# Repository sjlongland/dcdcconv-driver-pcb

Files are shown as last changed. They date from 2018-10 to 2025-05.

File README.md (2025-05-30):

[Find this project on codeberg](https://codeberg.org/sjlongland/dcdcconv-driver-pcb)

As a result of Github's decision to force AI-generated issues with no opt-out,
I am migrating personal projects of mine to Codeberg.  The project at Github
will be archived.

----

# PWM MOSFET driver board

This is a LVDS-compatible MOSFET driver board for use with the [DC-DC converter
board](https://codeberg.org/sjlongland/dcdcconv-controller-pcb).  It can drive
two N-Channel MOSFETs, either mounting the leads through the supplied
connection points `J3` and `J4` (suitable for TO-220 size MOSFETs) or via short
connection cables.  Due to parasitic inductance, it is best these be kept as
short as practical.

## Parts list

* U1: TI DS90C402 dual-channel LVDS receiver
* U2: TI UCC27212A-Q1 high/low side N-MOSFET driver
* U3: 74AHC04 (SOIC-14) hex inverting buffer (U1 when not connected to a LVDS
  source will drive both its outputs high, this inverts this to ensure both MOSFETs
  remain off in this condition.)
* C2: ≥100µF ≥10V electrolytic capacitor 6.3mm SMD (Bulk 5V rail decoupling)
* C1, C10: 100nF ≥10V ceramic capacitor 0805 SMD (local decoupling for U1, U3)
* C3: ≥100µF ≥20V electrolytic capacitor 6.3mm SMD (Bulk 12V rail decoupling)
* C4: 100nF ≥20V ceramic capacitor 0805 SMD (local decoupling for U2)
* C5: Bootstrap electrolyic capacitor for U2, refer to data sheet.  6.3mm SMD.
* J1: 6-pin 2.54mm "KK" connector (LVDS input and 5V rail)
* J2: 2-pin 2.54mm "KK" connector (12V rail)
* J3, J4: 3-pin 2.54mm "KK" connector or TO-220 size MOSFETs with heatsinks.
* (**FIT ONE ONLY**) C6, C7, C8, C9: ~100pF ≥20V ceramic capacitor 0805 (0V AC
  de-coupling to chassis.  Choose the one that best suits your mounting
  requirements.)

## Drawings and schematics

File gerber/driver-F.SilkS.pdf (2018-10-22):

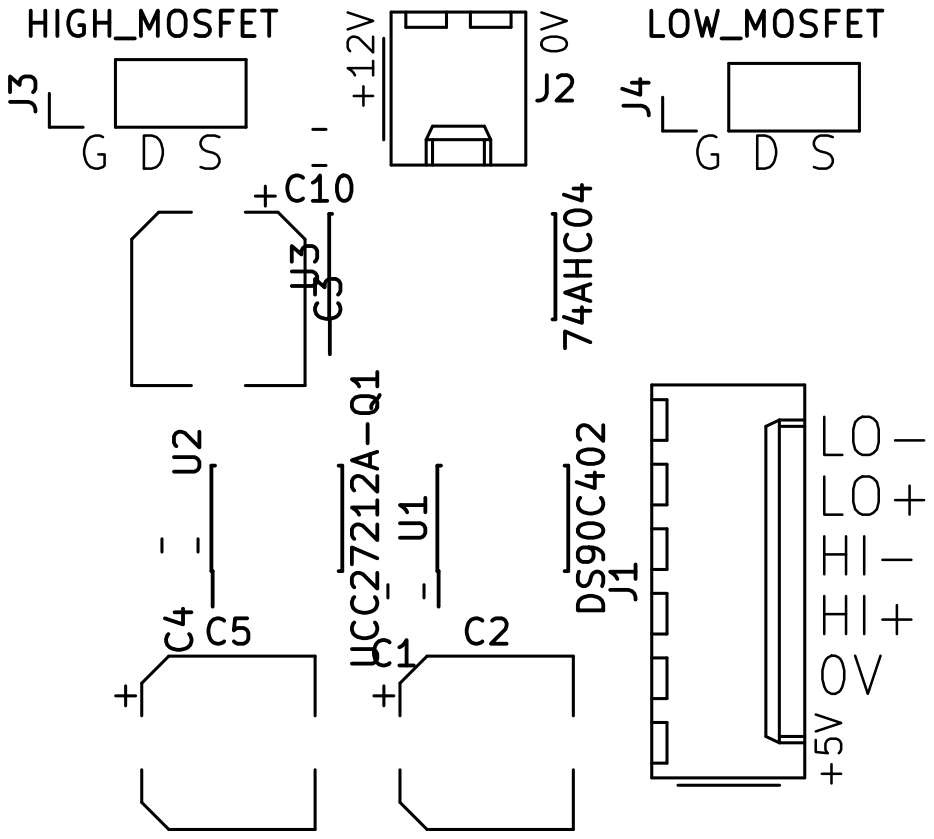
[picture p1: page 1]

File: driver.kicad_pcb Sheet: +5V LO- LO+ HI- HI+

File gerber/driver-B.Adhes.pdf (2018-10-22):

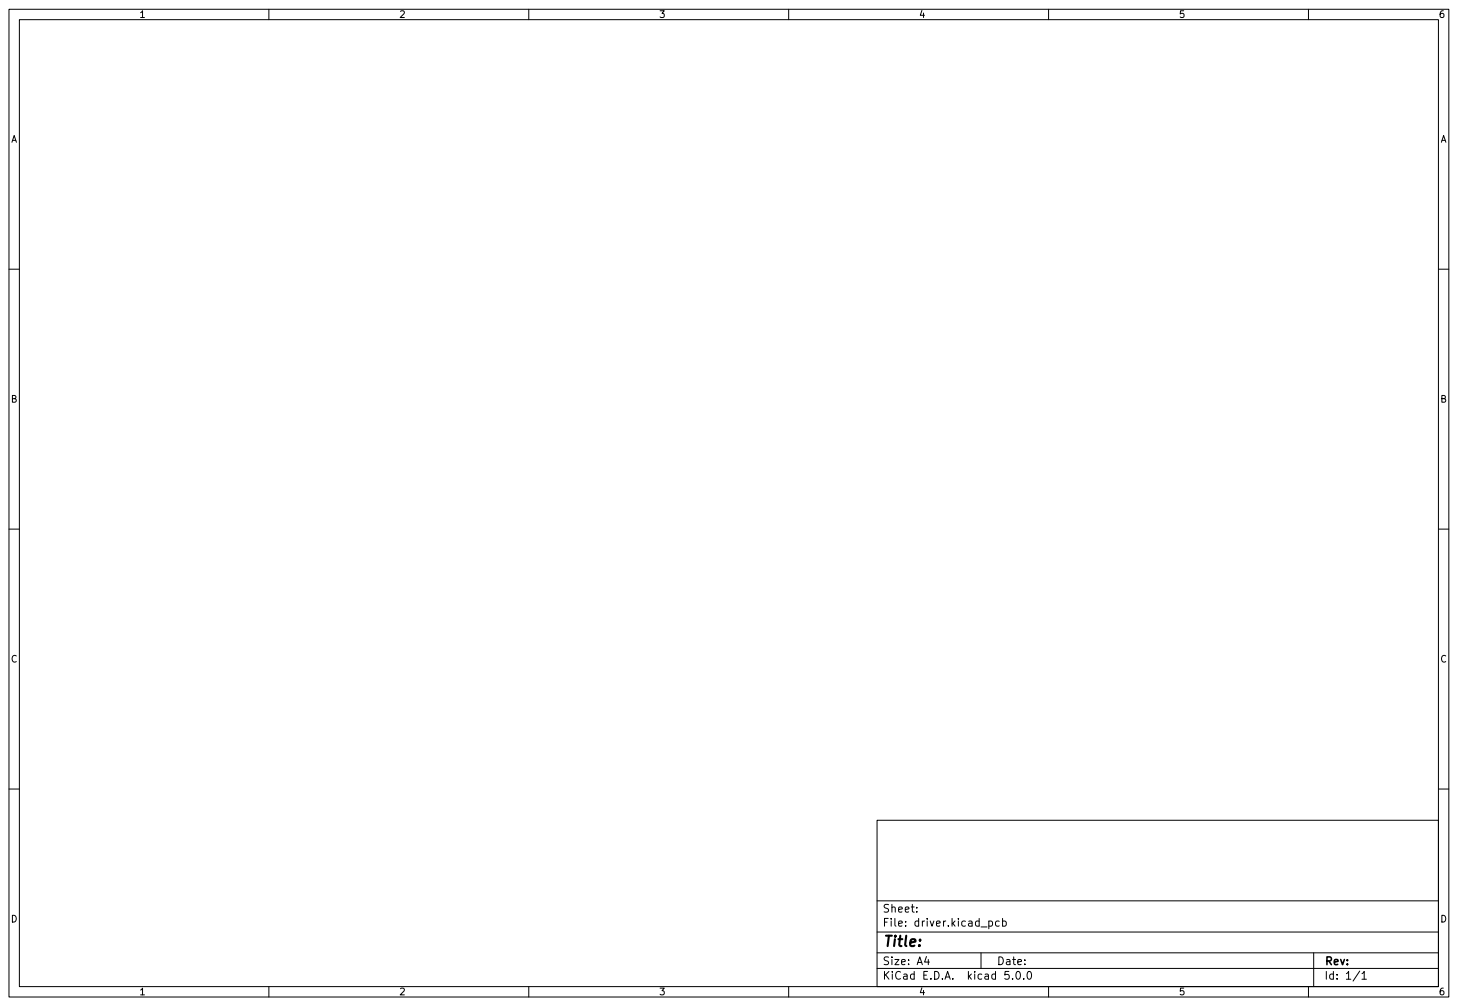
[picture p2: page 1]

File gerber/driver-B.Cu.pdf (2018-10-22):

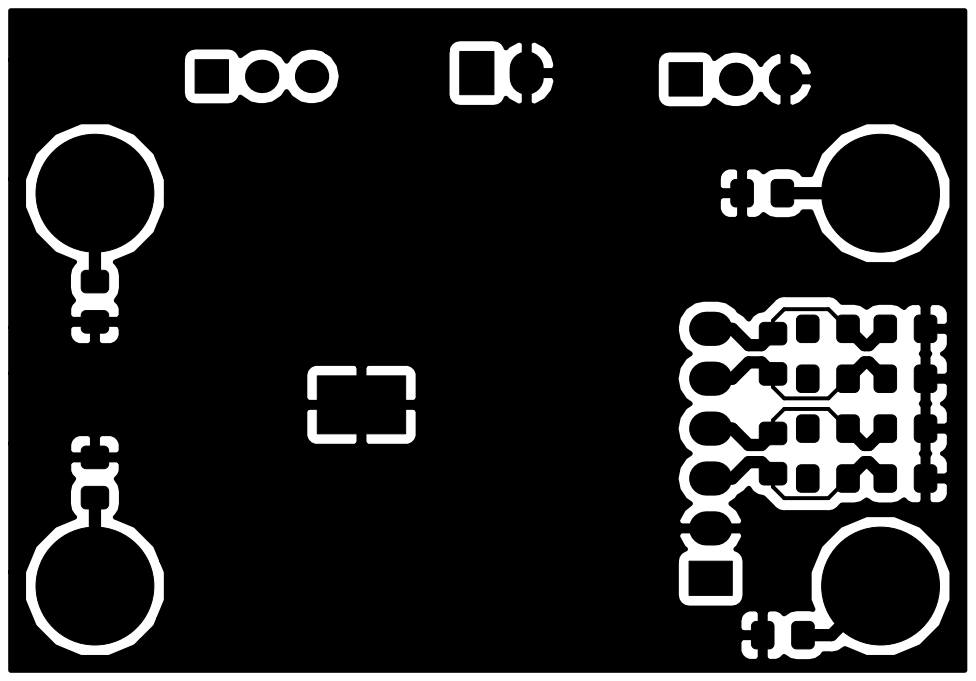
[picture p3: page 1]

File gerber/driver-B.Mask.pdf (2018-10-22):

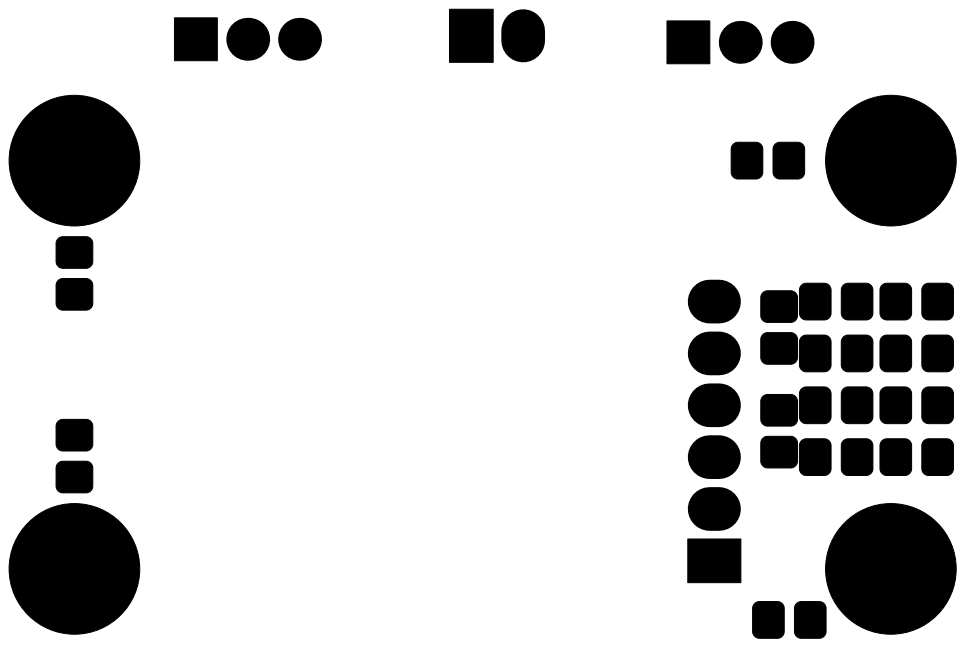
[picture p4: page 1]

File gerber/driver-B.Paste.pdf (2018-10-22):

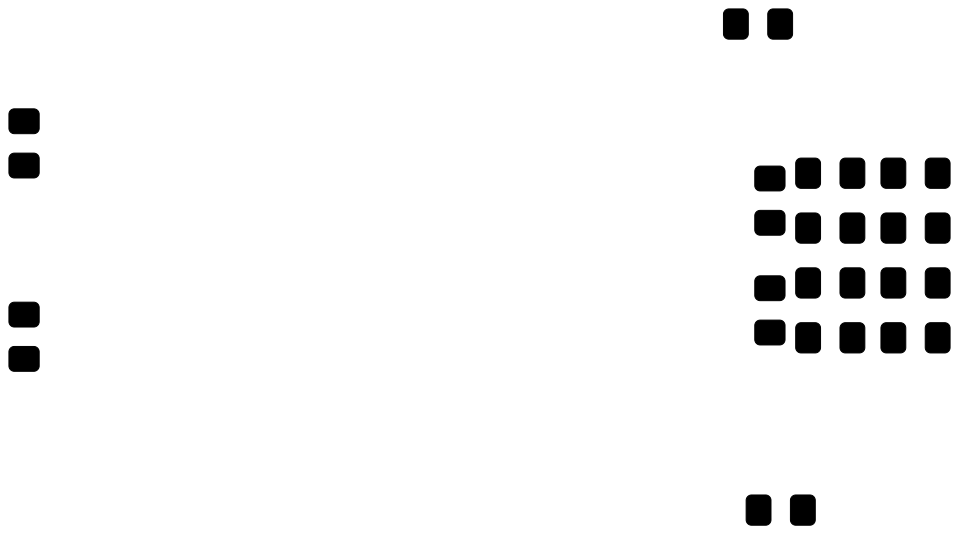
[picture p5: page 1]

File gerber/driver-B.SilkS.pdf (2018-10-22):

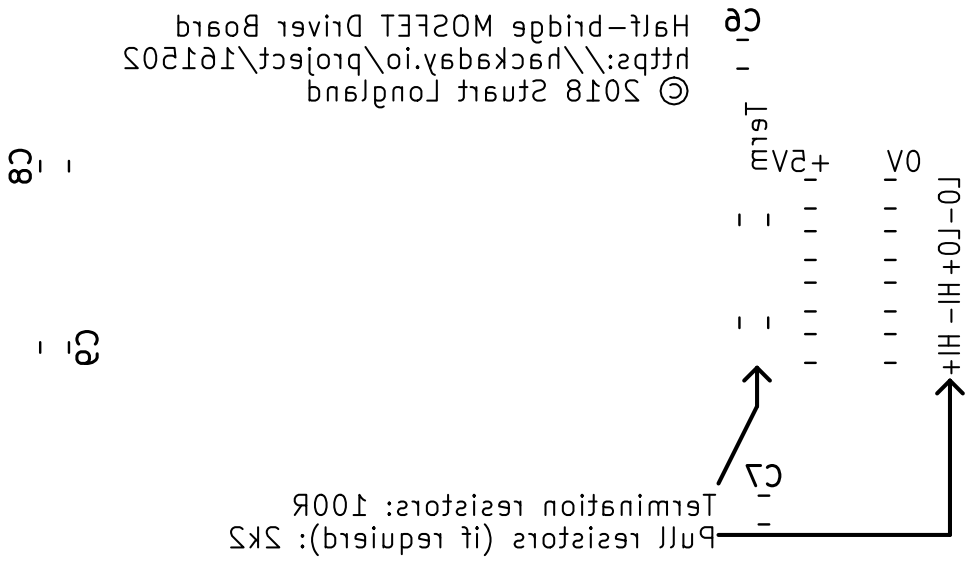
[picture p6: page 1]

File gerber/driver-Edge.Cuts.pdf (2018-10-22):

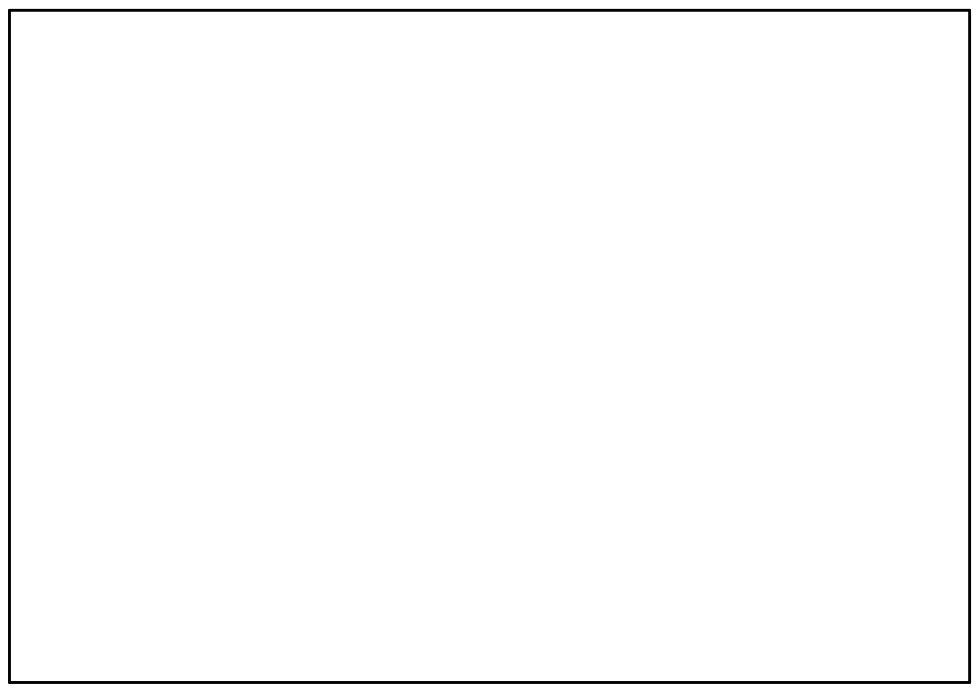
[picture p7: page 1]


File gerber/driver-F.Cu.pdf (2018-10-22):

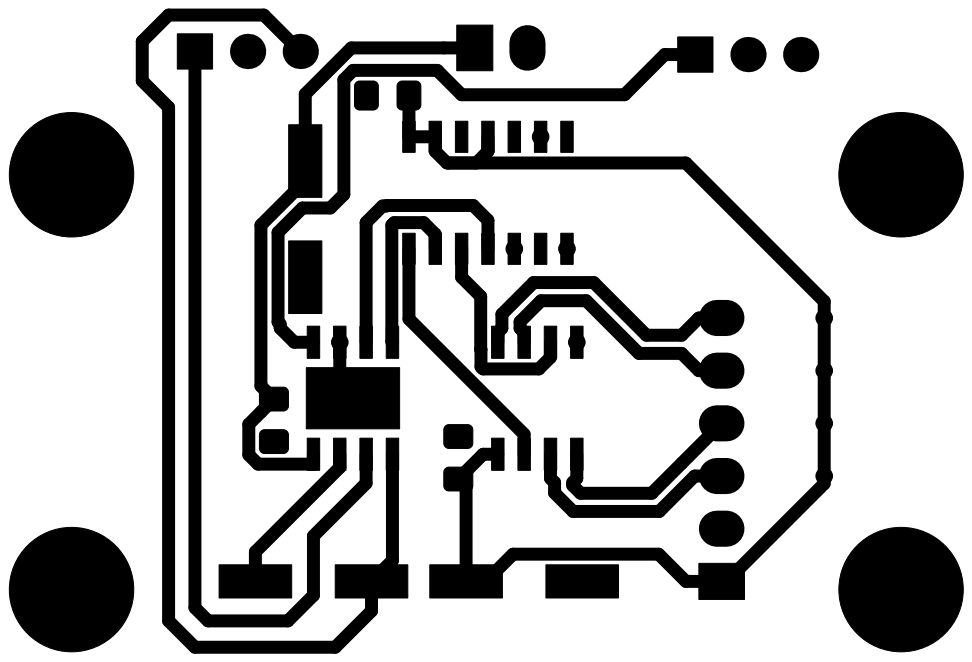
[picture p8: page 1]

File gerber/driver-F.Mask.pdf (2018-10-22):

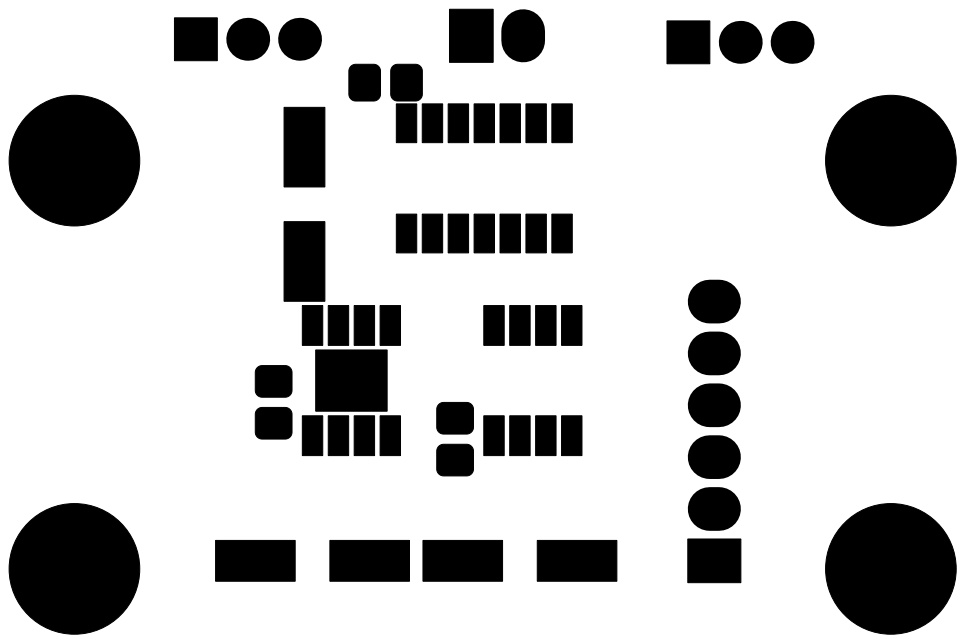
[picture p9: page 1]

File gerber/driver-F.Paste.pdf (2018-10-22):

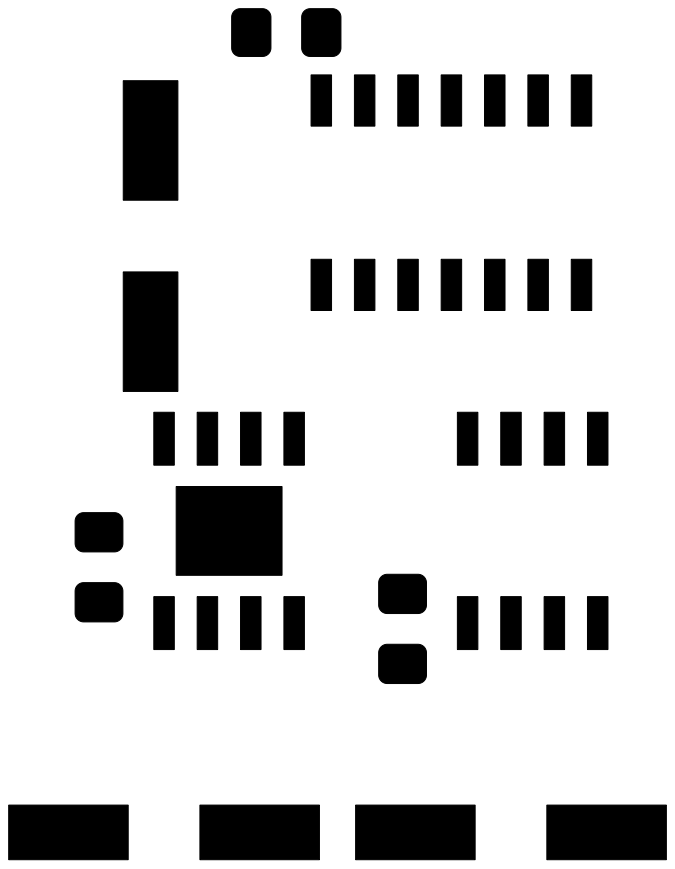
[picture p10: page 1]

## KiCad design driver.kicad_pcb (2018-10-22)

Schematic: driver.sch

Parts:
C1, C4, C10: 100n; C_0805_2012Metric_Pad1.15x1.40mm_HandSolder
C2, C3: 100u; CP_Elec_6.3x9.9
C5: CP; CP_Elec_6.3x9.9
C6, C7, C8, C9: 100p; C_0805_2012Metric_Pad1.15x1.40mm_HandSolder
J1: CTRL; Molex_KK-254_AE-6410-06A_1x06_P2.54mm_Vertical
J2: 12V_IN; Molex_KK-254_AE-6410-02A_1x02_P2.54mm_Vertical
J3: HIGH_MOSFET; PinHeader_1x03_P2.54mm_Vertical
J4: LOW_MOSFET; PinHeader_1x03_P2.54mm_Vertical
MH1, MH2, MH3, MH4: MountingHole_Pad; MountingHole_3mm_Pad_Via
R1, R2, R3, R4, R5, R6, R7, R8: 2k2; R_0805_2012Metric_Pad1.15x1.40mm_HandSolder
R9, R10: 100R; R_0805_2012Metric_Pad1.15x1.40mm_HandSolder
U1: DS90C402; SOIC-8_3.9x4.9mm_P1.27mm
U2: UCC27212A-Q1; TI_SO-PowerPAD-8_ThermalVias
U3: 74AHC04; SOIC-14_3.9x8.7mm_P1.27mm

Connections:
+5V: C1.1, C2.1, C10.1, J1.1, R1.1, R3.1, R5.1, R7.1, U1.1, U3.11, U3.13, U3.14 (VCC)
+12V: C3.1, C4.1, J2.1, U2.1
/HI+: J1.3, R1.2, R2.1, R9.2, U1.3
/HI-: J1.4, R3.2, R4.1, R9.1, U1.4
/HI_GATE: J3.1, U2.3
/HI_SRC: C5.2, J3.3, U2.4
/LO+: J1.5, R5.2, R6.1, R10.2, U1.7
/LO-: J1.6, R7.2, R8.1, R10.1, U1.8
/LO_GATE: J4.1, U2.8
/~HI~: U1.2, U3.1
/~LO~: U1.6, U3.3
GND: C1.2, C2.2, C3.2, C4.2, C6.2, C7.2, C8.2, C9.2, C10.2, J1.2, J2.2, J4.3, R2.2, R4.2, R6.2, R8.2, U1.5, U2.7, U2.9, U3.5, U3.7 (GND), U3.9
unnamed: C5.1, U2.2
unnamed: C6.1, MH1.1
unnamed: C7.1, MH2.1
unnamed: C8.1, MH3.1
unnamed: C9.1, MH4.1
unnamed: U2.5, U3.2
unnamed: U2.6, U3.4

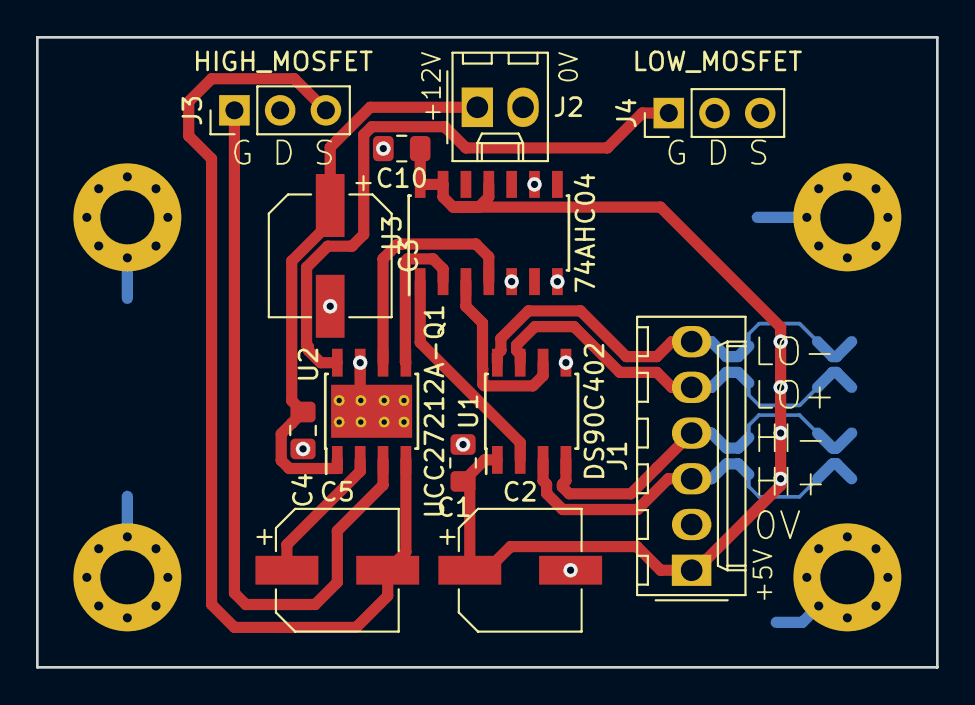
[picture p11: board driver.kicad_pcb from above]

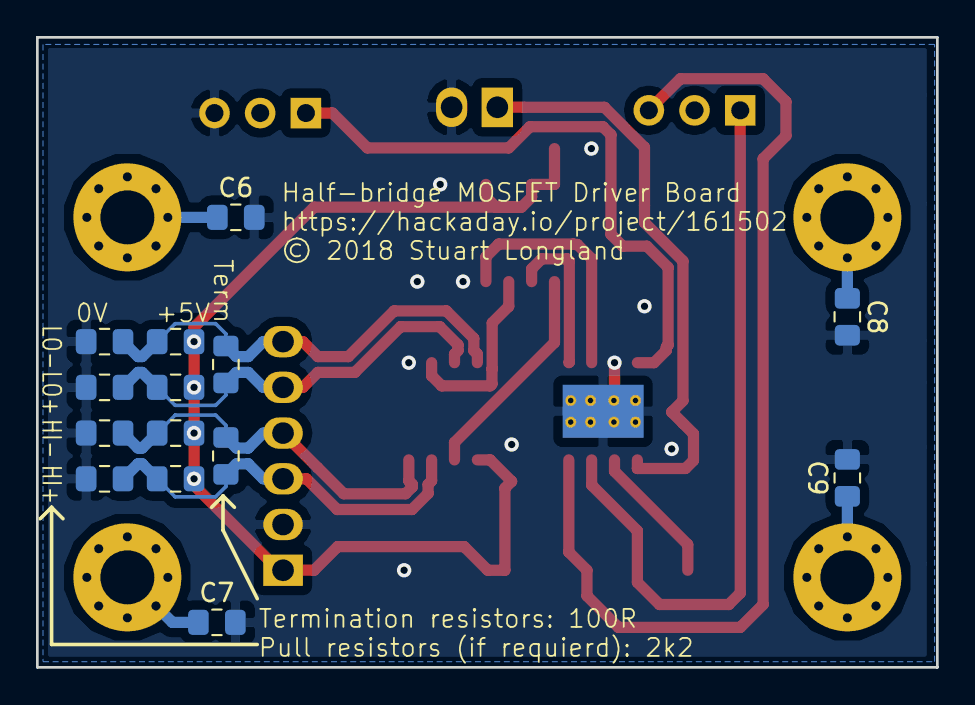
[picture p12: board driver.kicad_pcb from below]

Board: 2 copper layers, 50.0 x 35.0 mm, 31 parts (14 on the bottom side), 19 nets.

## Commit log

2018-10-07 Initial check-in
    [driver.kicad_pcb, driver.sch]
2018-10-22 pcb: Finalise for prototype run.
    [driver.kicad_pcb]
2018-10-22 gerber: Add CAM production files.
    [driver-B.Cu.gbl, driver-B.Mask.gbs, driver-B.Paste.gbp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]

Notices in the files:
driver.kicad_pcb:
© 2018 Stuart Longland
